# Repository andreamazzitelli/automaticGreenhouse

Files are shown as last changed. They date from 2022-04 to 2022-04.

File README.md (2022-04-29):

# automaticGreenhouse
This is the repository for the Internet of Thing 2021/2022 of the Master in Computer Science, La Sapienza Università di Roma

# General Description
The scope of the project is to create an automatic greenhouse that can act on the environment in which a plant is living to tailor the living space to the plant’s needs. By monitoring the environment, it’s possible to learn in real time the conditions in which the plant is living. In particular, the system measures those aspects that are fundamental to a plant, these being temperature, humidity and soil moisture. Knowing this information, the system can promptly act in several ways: opening or closing the water, turning on and off a heating lamp or by keeping the light always on. 

## Sensors
So to take the measurements needed by the system the following two sensors were selected:
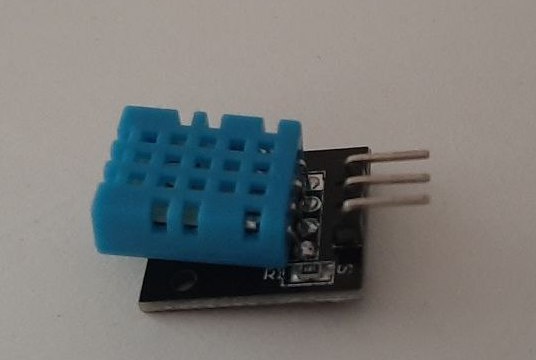
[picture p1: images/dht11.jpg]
dht11
- ***DHT11 Humidity and Temperature***: <br> this sensor collects information on the temperature and on the air’s humidity and gives them to the system using an analog output. In particular, for the temperature it has a range of 0-50°C with an accuracy of +/- 2°C with a precision of 8 bits; and for the humidity we have a range of 20-90% RH (RH stands for Relative Humidity) with an accuracy of +/- 5% RH with a resolution of 8 bits (the datasheet can be found here [DHT11 Datasheet](https://www.mouser.com/datasheet/2/758/DHT11-Technical-Data-Sheet-Translated-Version-1143054.pdf)).

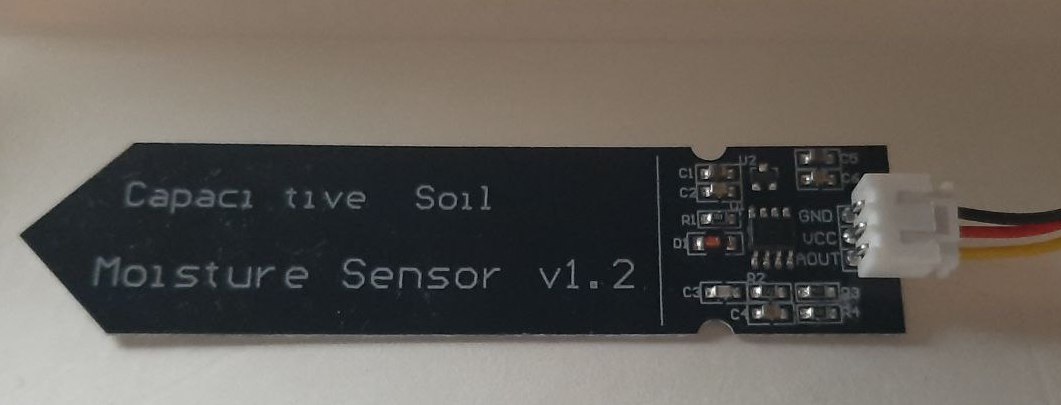
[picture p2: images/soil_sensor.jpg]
soil_sensot
- ***Soil Humidity Sensor***: <br> this sensor collects information on the soil moisture using capacitive sensing (i.e its capacitance changes depending on how much moisture is present in the soil), it gives its output to the system as analog input (the datasheet can found here [Soil Humidity Sensor Datasheet](https://cdn.shopify.com/s/files/1/1509/1638/files/Hygrometer_V1.2_Sensor_Modul_Datenblatt_AZ-Delivery_Vertriebs_GmbH.pdf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)).

The sensing done by the sensor is periodic because the system needs to continuously evaluate the environment in which the plant is living, indeed an event-driven one would not make sense taking into account the analogical nature of what the system measures (i.e temperature …). In particular the interval at which the sensors take their measurements is 15 seconds so that the system can always be updated without being overloaded with values.<br>
It is important that these sensors work independently even if the aspect they measure may depend on each other. For example air humidity may depend on the moisture in the soil but it also decreases with high temperature, for this reason the sensors must work in parallel to provide a correct and continuous evaluation of the environment. In the code this separation is achieved using threads.

## Actuators
To act on the environment the following two actuators were selected:
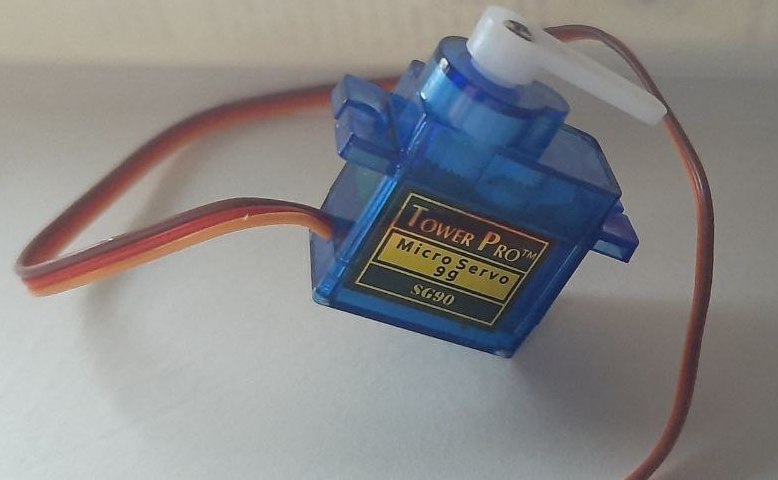
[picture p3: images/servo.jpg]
servo_motor
- ***Servo Motor SG90***: <br> the servo motor open and closes the water, for this reason it’s activation/deactivation depends on the values detected by the soil moisture sensor so to keep the humidity of the soil between 20% and 60% (that is the adequate percentage for most types of plants). More precisely the servo opens the water when the soil moisture gets lower than 20% and turn off the water when the moisture gets higher than 60%. (the datasheet can be found here [Servo Motor Datasheet](http://www.ee.ic.ac.uk/pcheung/teaching/DE1_EE/stores/sg90_datasheet.pdf))<br> To made use of a servo motor in this way I used the a 3D printed servo valve that can be found at this [LINK](https://www.thingiverse.com/thing:4876444),

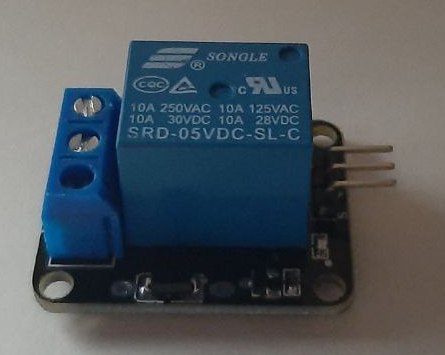
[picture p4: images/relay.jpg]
relay
- ***Relay Module 5V/250VAC***: <br>the relay instead can be used in several ways depending on what the user goal is, but in general is used to keep the temperature above a certain threshold by turning on and off a heating bulb. More precisely it is turned on if the temperature sensed by the dht11 sensor gets lower that (goal_temperature -10%) and is turned off if the value gets higher that (goal_temperature +10%). The +/- 10% are needed to avoid the relay to keep switching on and off due to very small changes in temperature (the datasheet can be found here: [Relay Datasheet](https://components101.com/switches/5v-single-channel-relay-module-pinout-features-applications-working-datasheet))

The activation or deactivation of these actuators can be done manually by the user, but by default is done in an automatic way. 

### Data Processed on the by the Board
In general the amount of the data received from the sensors depends on how well the threads that handle the measurement are synchronized. If they are perfectly in sync, then the system would receive a total of 24 bits (8 bits for temperature, 8 bits for relative humidity and 8 bits for soil moisture). <br><br>
This data is then formatted in a message that is then sent to the broker. In particular to reduce the number of bytes sent by the device in the network the message has a payload size of 9 bytes when sending data about temperature and humidity, and size of 5 bytes when sending data about soil moisture. Obviously in addition to the payload the message has a header but in this case is small thanks to the use of mqtt-sn protocol.

# System Architecture
In the following section the architecture of the whole system will be described starting from an overall view of the network components, then analyzing all the cloud aspects, and in conclusion there will be a brief description of how the sensors and actuators are connected to the board.
<br>
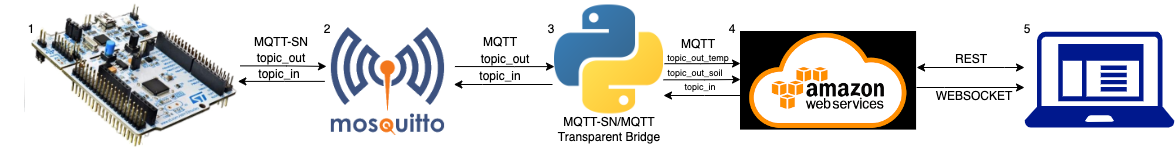
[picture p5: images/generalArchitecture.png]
generalArchitecture

<br>
The general architecture of the network can be described as a chain of blocks that exchange messages; this structure is shown in the image above. More in detail the block that compose the system are:
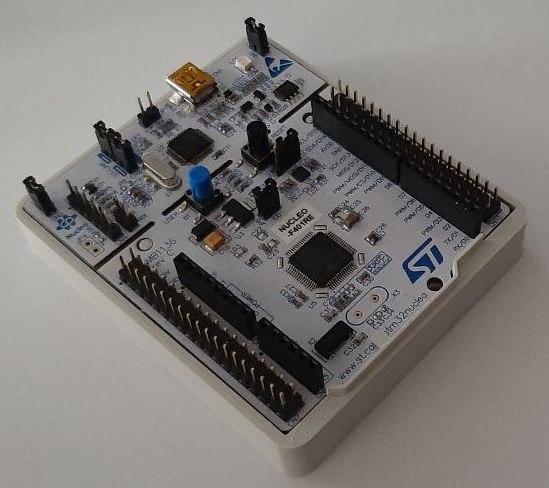
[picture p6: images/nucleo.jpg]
nucleo_board
1. ***Nucleo-f401re Board***: <br> it generates and sends data to the broker that is in the next block of the chain using mqtt-sn, it publishes the messages on the topic “topic_out”. Moreover it is subscribed to the topic “topic_in” of the broker in the next block where it reads the instructions that are sent by the user.

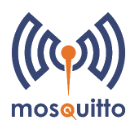
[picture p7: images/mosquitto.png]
mosquitto
2. ***MOSQUITTO***: <br> it is a MQTT-SN/MQTT message broker that is the closest block to the board. Indeed, it interacts directly with it. In particular it stores the messages coming from the board in the topic “topic_out” and those going to the board in the topic “topic_in”. In theory any mqtt-sn/mqtt broker can have this role.

3. ***MQTT-SN/MQTT TRANSPARENT BRIDGE***: python <br> it is a python script that works as a bridge exchanging messages using MQTT between the broker in the previous block and the broker on the cloud in the next block of the chain. <br><br> It is subscribed to both the topic “topic_in” of the cloud broker (in the next block) and to the topic “topic_out” of the previous block broker. Indeed when a message is published on the “topic_in” of the cloud broker the transparent bridge reads it and publishes it on the previous block’s broker. Something similar happens when a message is published on the “topic_out” of the previous block, the bridge reads this new publication and publishes it into the cloud broker. <br> <br>Regarding the publishing of messages in the adjacent blocks we have a peculiarity, this block performs some edge computation. Indeed it has the role of changing the format of the messages to make them more suitable for the blocks it is bridging. In particular it does the following: 
   - messages coming from the previous block and going to the next one, it expands them turning the small payload more suitable for a mqtt-sn communication into a proper json object so that the cloud functions can easily work with it.
   - messages coming from the next block and going to the previous one, it compresses the json object into a smaller message so to reduce the payload size so that it can consume less bandwidth and be easily handled by the previous block in the chain.<br><br>
Moreover we have another peculiarity in how the messages are published on the cloud mqtt broker indeed in this case the messages are published on two different topics of the cloud broker: “topic_out_temp” and “topic_out_soil” in this way is easier to separate and elaborate the messages coming from different sensors.

4. ***Amazon Web Services***: aws_logo<br> is the cloud part of the system. All the data received from the previous block on the topic “topic_out_temp” and “topic_out_soil” is processed, stored and then made available to the user using API REST. Moreover the user can send commands using API REST that publish the command on the topic “topic_in” of the cloud broker where it will be red by the previous block. (Obviously any cloud service provider correctly configured would work the same)

5. ***Web Application***: <br> last block of the chain. Allows the user to visualize the data collected by the system and interact with it. In particular using charts the user can see not only the measurements of the last hour but also see them almost in real time (we need to take into account the latency needed by the data to go from the board to the cloud services). Moreover some aggregated values are provided to the user like: the average, minimum and maximum values and the variation.

<div>
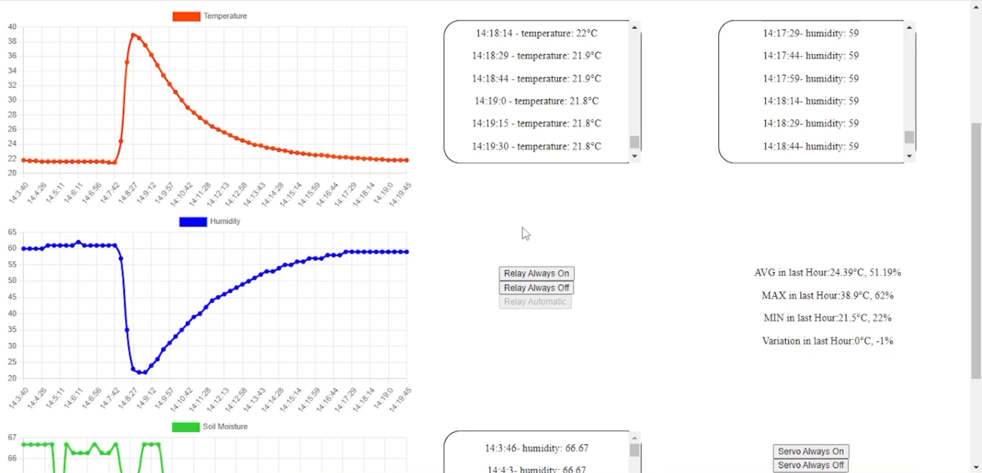
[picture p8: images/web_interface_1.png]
web1
   
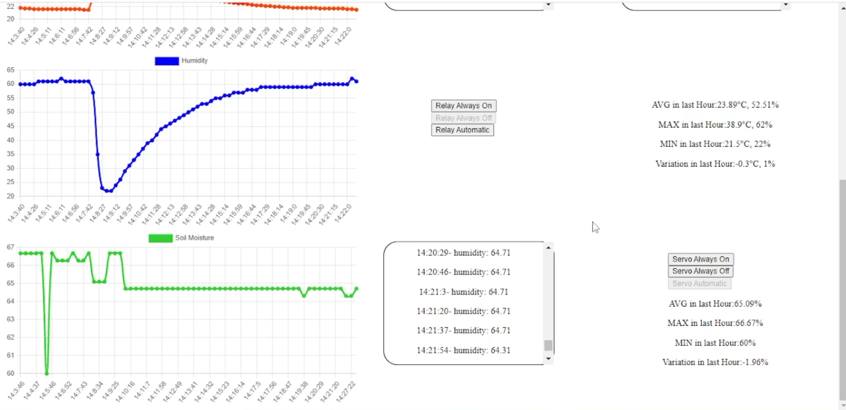
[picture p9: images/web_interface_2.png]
web2
   
</div>

### Cloud Services

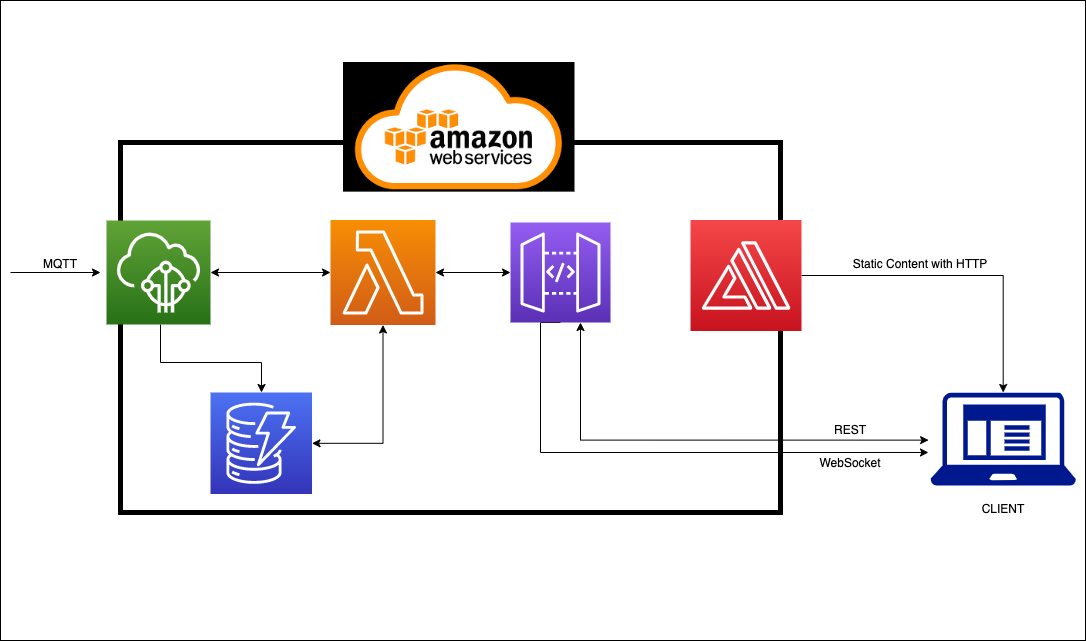
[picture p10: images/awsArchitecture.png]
awsArchitecture


As already mentioned the cloud service provider used is Amazon Web Services. In particular the services used are:
- ***Iot Core***: iot_core<br> whose main role is to work as a mqtt broker where messages are published. Moreover, the rule engine of the service allowed us to directly act on the incoming messages, saving them on the DB and invoking functions when a new message arrives.
- ***DynamoDB***: dynamoDB_logo<br> database where every data received from the board is stored. In particular it has 2 tables to store the information received and 1 used to keep track of the connections to the websocket service.
- ***Lambda***: lambda_logo<br> that allows us to write the functions for several purposes like: interact with the database, publish messages on a broker, handle the websocket (connection, disconnection and new information on the status). In particular it has 2 functions to read the data of the sensors (one per table), 1 function to publish messages on a broker, 3 functions to handle the websocket.
- ***API Gateway***: api_gateway<br> to create and publish both the REST API and the WebSocket API
- ***AWS Amplify***: amplify<br> to provide the web application’s static content to the user 

<br><br>
***NOTE: on april 2022 AWS introduced the Lambda Function URLs that makes the use of API Gateway not strictly needed. Indeed is possible to use this new functionality to obtain an endpoint for a Lambda function and directly call the function skipping the creation of a new API, at least for the REST ones. In theory is easy to introduce Lambda URLs in this project simply by subbstituting the call to the Gateways' APIs with a call the the Lambda URL but futher testing would be required*** <br><br>

Now is possible to analyze the interaction with AWS from the point of view of the IoT Core broker receiving a message and from the one of a user accessing the web interface. <br>In the former we have that once the broker receives a message, it is received either on the “topic_out_temp” or on the “topic_out_soil” topic, in both cases two things happens: the information is stored in the corresponding table and the lambda function sends a messages with the data to all active connections on the websocket.<br><br> In the latter we have that the user asks to AWS Amplify using https for the static components of the web application, as soon as these are loaded the javascript in the web page does two things: invokes the REST API to obtain the data stored in the DynamoDB tables and connects to the websocket provided by an API of the API Gateway. <br>In this way the client has the data from the last hour and is kept updated thanks to the websocket. <br>Moreover from the web application the user has the ability by pressing some buttons to invoke an API that invokes a lambda function that publishes a message with a command to the board on the cloud broker.

### Connections to the Board
[Here](https://github.com/andreamazzitelli/automaticGreenhouse/raw/main/images/automaticGreenhouseCircuit.fzz) the link to fritzing circuit 
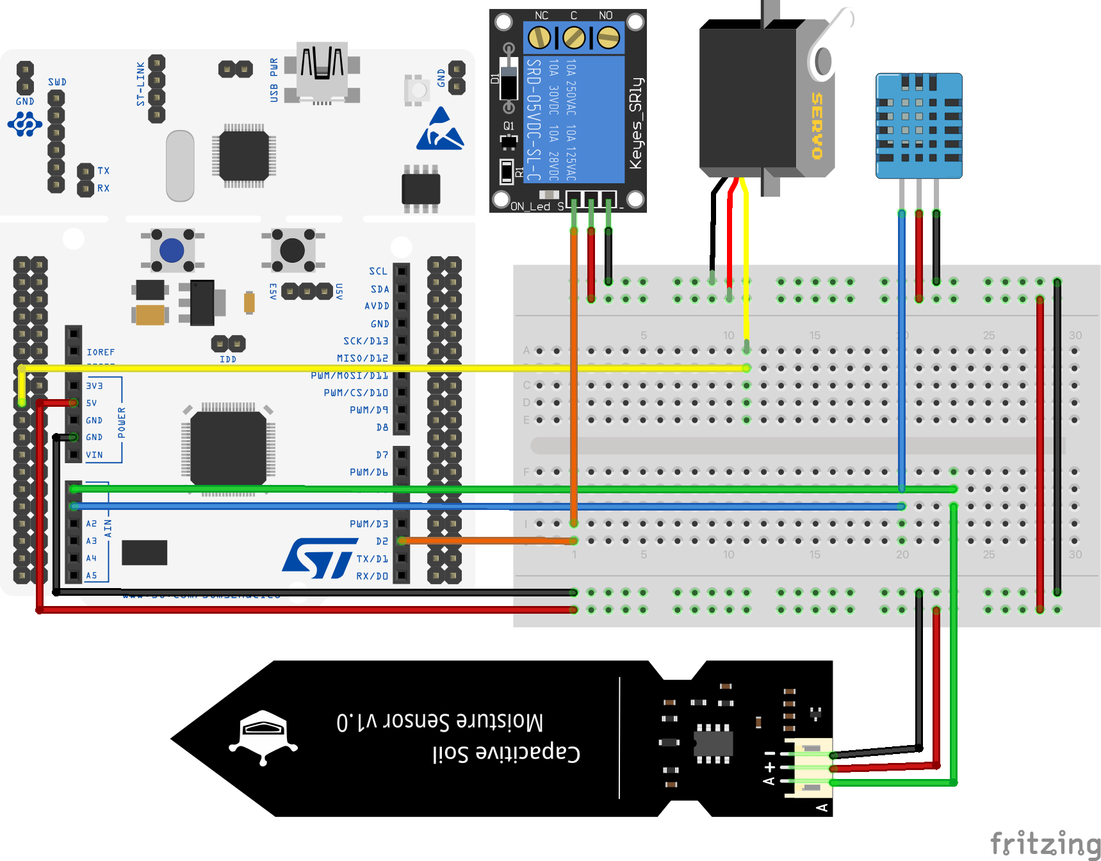
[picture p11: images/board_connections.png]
board connections

So to conclude this section a brief description on how the board, sensors and actuator are connected. The connections are rather simple as is possible to see from the above image:

pin board<br>

- All the sensors and actuators are connected to Ground and 5V
- the relay module is connected to the digital pin Arduino pin D2(PA10 on the board)
- the servo motor is connected to the pin PA15 a PWM pin
- the dht11 sensor is connected to analog pin A1
- the capacitive soil moisture sensor is connected to analog pin A0 

(the position of the pins on the board can be see on the pinout image on the left)<br>
Obviously the board is connected to a laptop so that it can get power and use the ethos (ethernet-over-serial)  mechanism.

### Network Performances
Using a tool to analyze packets in the network (like wireshark) is possible to see how the network is affected by the message exchanged by the several components. Indeed the most problematic part of the connection is the link between the board and the mosquitto broker. In particular we have that the network traffic happening using UDP between these two components is:
- 33 bytes for sending data from the soil moisture sensor 
- 37 bytes for sending the data from the dht11 sensor. 

Assuming that the threads handling these measurements are synchronized we can say that a total of circa 16,8 kb per hour are generated and the needed bandwidth to run the system is of at least 4,7 bytes per second. <br><br>
Even if the bandwidth required to run the system is low for today's standards in some situations it may be needed to reduce even more the data transmitted. This is achievable if the transmission interval is increased, but in this the data collected on the cloud is less representative of the real state of the environment. To avoid this loss in accuracy the system could aggregate data on the node, for example at every timeout it does not send the last value sensed by the sensor but the average of the previous interval. So there is a clear tradeoff between the amount of data transmitted on the network and the system’s accuracy.<br><br>
The other link of interest is the one between the mosquitto broker and the cloud service provider. The main aspect here is that in the middle there is the transparent bridge that acts on the messages. However even if the message size increases and the protocol used to exchange messages is TCP (that uses in general more messages than UDP), the operation done by the transparent bridge are done on the edge. For this reason, the presence of a more reliable bandwidth is almost guaranteed.<br><br>
***Latency***: instead regarding the latency of the system we have that usually is under 2s from when the sensor register a new value and to when this new value appears on the web application, the same is true for the other direction: there is a latency under 2s from when a button is clicked on the web app to when the system acts accordingly. <br>This latency in a case like this is not a problem at all, indeed the system does not have strict requirements neither on how fast to act when a command is sent by the user nor on how fast the data must be shown to the user. Mainly this is due to what the system is though for, indeed under normal circumstances is rare for values like temperature and humidity to drastically change and even if we are in those rare circumstances, excluding the user response time, 4s is small enough to prevent "damages".

# WALKTHROUGH
The first steps to do are:
- download and setup RIOT OS as described in the official documentation ([RIOT OFFICIAL DOCUMENTATION](https://doc.riot-os.org/getting-started.html))
- download and setup the mosquitto broker as described in the official documentation ([DOCUMENTATION](https://github.com/eclipse/mosquitto.rsmb))
- download this repository

### Cluod Setup
- ***DynamoDB***: create 3 tables: 
   1. connection_table with Partition Key a string called“connection_id”
   2. soil_humidity_table with Partition Key a number called “id”
   3. temperature_table with Partition Key a number called “id”
- ***Lambda***: create 6 lambda functions choosing as language Node.js 14.x where to paste the code provided in this repository under the aws directory (see later for a brief description on how to add permission to a lambda function):
   1. connect: where to paste the code found in aws/connect.js and needs to have permission to access to DynamoDB
   2. disconnect: where to paste the code found in aws/disconnect.js and needs to have permission to access to DynamoDB
   3. publish2Broker where to paste the code found in aws/publish2Broker.js and and needs to have permission to access to IoT
   4. readTemeperature: where to paste the code found in aws/readTemperature.js and needs to have permission to access to DynamoDB
   5. readSoilHumidity: where to paste the code found in aws/readSoilHumidity.js and needs to have permission to access to DynamoDB
   6. readTemp4WebSocket: where to paste the code found in aws/readTemp4WebSocket.js and needs to have permission to access to DynamoDB, API Gateway and Execute API<br>
***NOTE: is fundamental to properly set up the permissions given to each function***

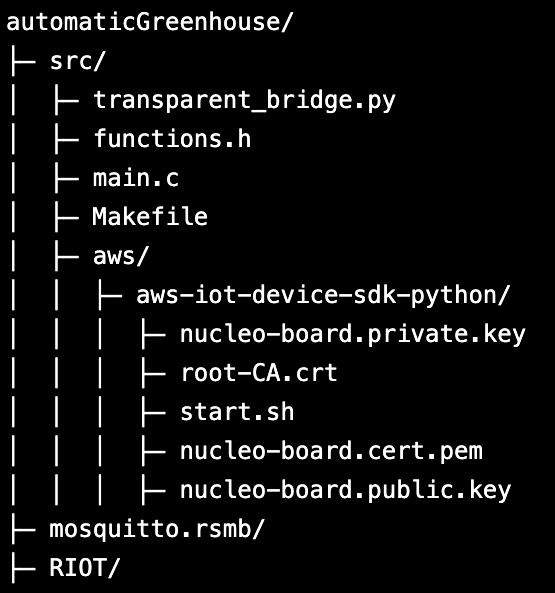
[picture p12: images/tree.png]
pin board
- ***IotCore***: click on “Connect a device” and follow the steps using as name of the thing "nucleo-board", at the end of the guided procedure it should have downloaded the following files: root-CA.crt, nucleo-board.cert.pem, nucleo-board.private.key. 
Now for the system to work build a directory like the one in the image on the right (all the file in the aws directory were downloaded after this first step of the IoTCore)
<br>
Now always from the IoT Core you need to go on Secure->Policies->nucleo-board-Policy then click on “Edit Active Policy” and append in the policy resource text area:
- in the first one: resource_arn:topic/topic_out_soil,resource_arn:topic/topic_out_temp,resource_arn:topic/topic_in (elements MUST be separate with a comma WITHOUT spaces in between),
- in the second one: resource_arn:topicfilter/topic_in,
- in the third one: resource_arn:client/nucleo,
Once this is done click on “Save as new version” and set it as active one. <br>

The next step is to configure the rules of the rule engine so go on Act->Rules, here you need to create two rules:
   - in the first one set the “Rule query statement” as “SELECT temperature, humidity FROM 'topic_out_temp' “ and add the action to “insert a message into DynamoDB” giving as table name “temperature_table”, Partition key “id” and as Partition Key Value “$(timestamp())” (this will create a new element in the table with id the epoch time). Once this action has been added click again “Add Action” and select “Send message to Lambda Function” selecting as lambda function readTemp4WebSocket
   - in the second one set the “Rule query statement” as “SELECT soil_humidity FROM 'topic_out_soil'”, also here add the same action as the other rule changing only the table name in “soil_humidity_table”

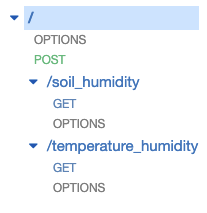
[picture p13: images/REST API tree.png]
rest api tree
- ***API Gateway***: there are 2 APIs needed:<br>
   - a WebSocket API called “sensors” with 4 routes each calling a lambda function: $connect that calls “connect”, $disconnect that calls “disconnect”, readTemp that calls “readTemp4WebSocket” and readSoil that also calls “readTEmp4WebSocket”.
   - a REST API also called sensors that has the structure in the image. In particular the POST on / should call the "publish2Broker" function, the GET on /soil_humidity should call "readSoilHumidity", the GET on /temperature_humidity should call "readTemperature". (take note of which are the endpoints of these resources because, because there will be needed on a later step)

- ***AWS Amplify***: first you need to edit the file index.html changing adding the link to your API in the following lines:
   - 372, inside the fetch add as a string the URL to the API that returns the values obtained from the dht11 sensor,
   - 382, inside the fetch add as a string the URL to the API that returns the values obtained from the soil moisture sensor,
   - 451 as first parameter inside the fetch add as a string the URL to the API that allows us to send commands to the board.
   
   Once this is done create a new project and load the index.html, index.js and style.css files that you find inside the directory web app of this repository

With this the AWS setup is done.

### Board Setup
The next steps are:
- connect the sensors to the board like shown in the previous image.
- connect the board to you machine
<br>
Now go to the mosquitto.rsmb/rsmb/src folder and execute the following command:

```
./broker_mqtt config.conf
```

and leave the broker running. <br>
Open a new terminal on MAIN/automaticGreenhouse and open the transparent_bridge.py and set the lines 8-11 to the requested value, save and close. Then execute:

```
python3 transparent_bridge.py
```

as before leave the bridge running and open a new terminal in the same  folder and execute 

```
make flash term
```

once the command is done i.e the serial monitor is shown, open a new terminal and execute the following command 

```
sudo ip a a 2000:2::1 dev tap0
```

then press the reset button on the board and after a few seconds if everything has been set up correctly the board should start to operate and on the 
application the measurement should be showing.

# BLOG POST: 
I decided to focus a specific aspect of the project: how to connect the nucleo-f401re to the cloud. <a href="https://www.hackster.io/mazzitelli1835022/connect-riot-os-with-the-cloud-4bf88a">Here's the link to the blogpost</a>
# Linkedin:
Here is my <a href="https://www.linkedin.com/in/andrea-mazzitelli/">Linkedin Account</a>
# YouTube Video:
To provide a better overview of the system and it's functionalities. The demo is not done in a real environment (i.e with sensors/actuators put inside a real greenhouse) becuase the phenomenon that the system sense usually does not drastically change in a brief period of time (both temperature and soil moisture need sometimes to increase or decrease). So for sake semplicity in showing the result, in the demo I manully alter the values sensed by either using an hairdryer on the temperature sensor or by forcing the soil moisture sensor to sense lower level of moisture.
Here is the link to the demo: <a href="https://youtu.be/zmuy0vqKZXE">YouTube Video</a>

# Photos
<div>
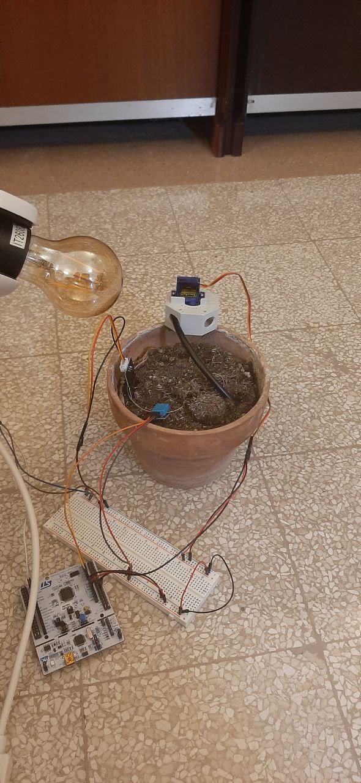
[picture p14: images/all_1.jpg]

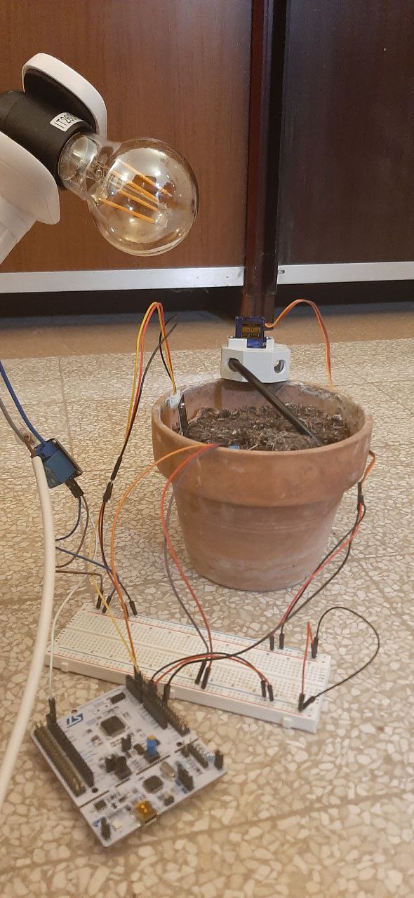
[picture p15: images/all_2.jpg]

</div><br>
<div>
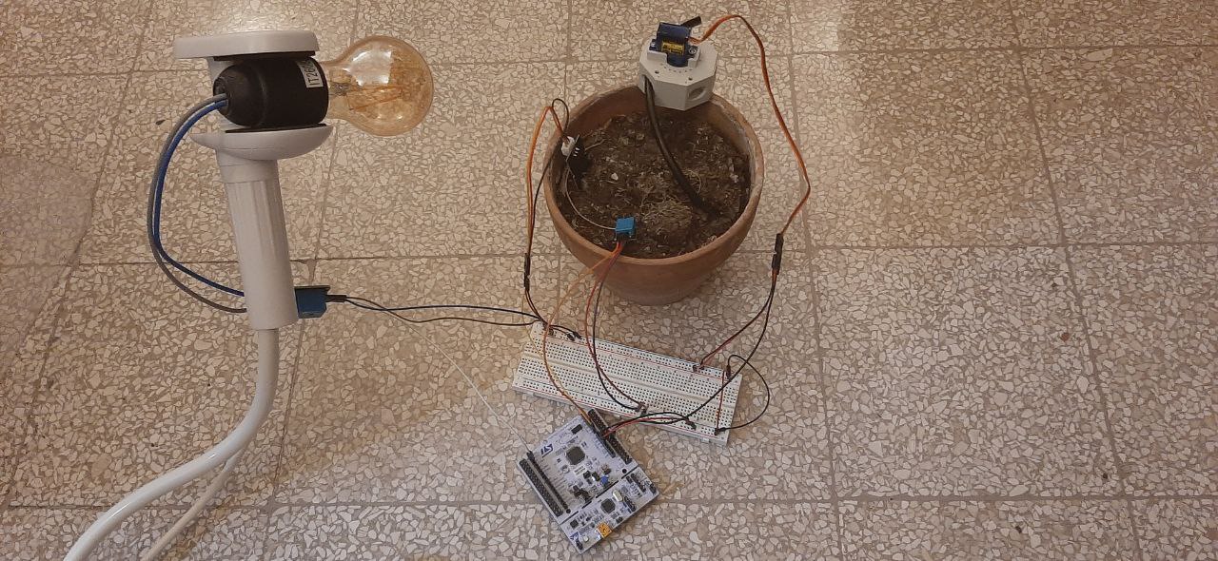
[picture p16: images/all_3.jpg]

</div><br>
<div>
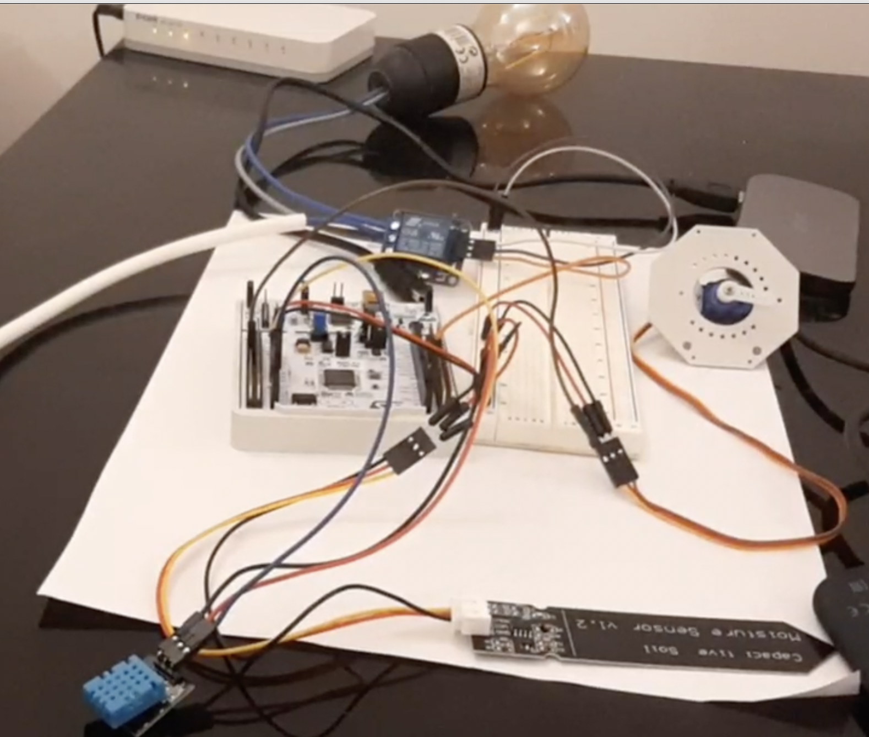
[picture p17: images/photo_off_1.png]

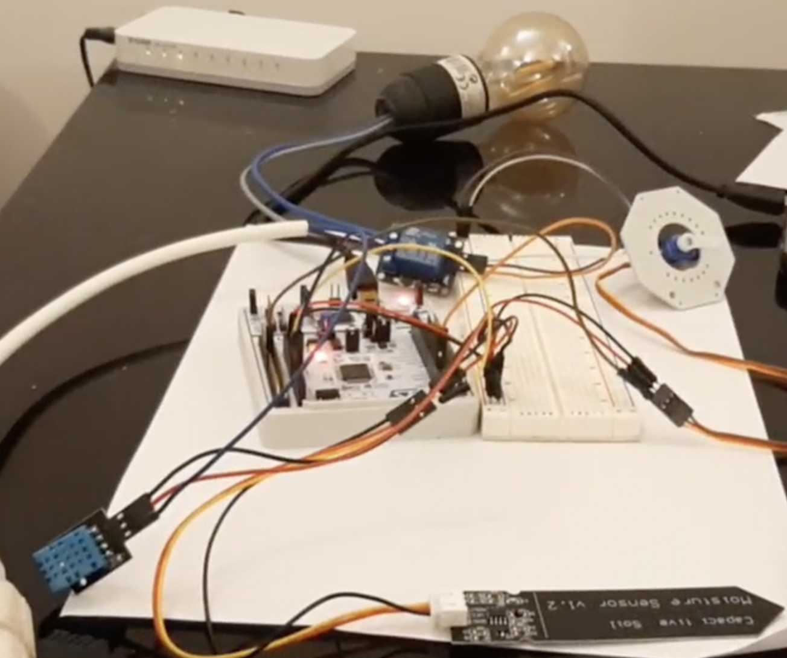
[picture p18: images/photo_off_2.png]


</div><br>
<div>
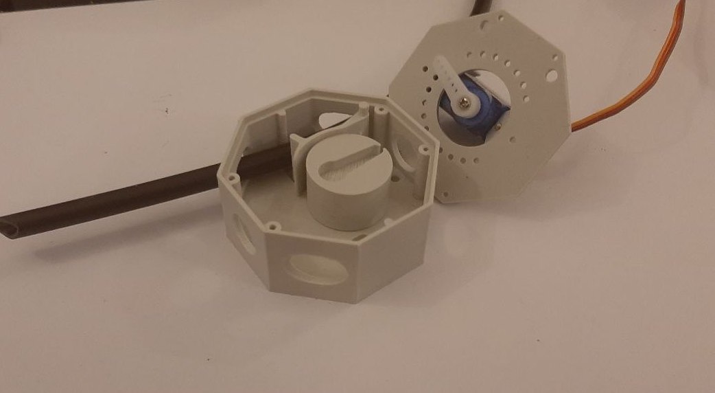
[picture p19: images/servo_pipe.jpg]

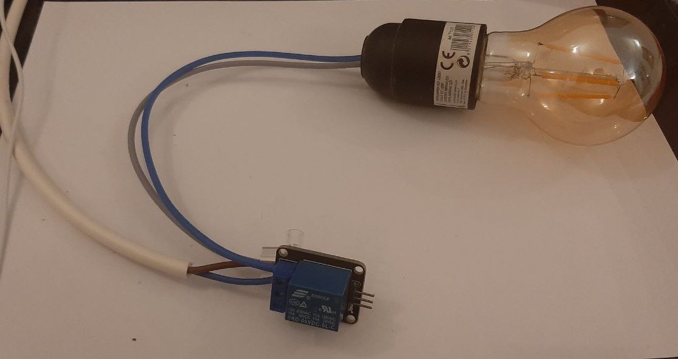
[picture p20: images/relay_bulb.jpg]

</div><br>

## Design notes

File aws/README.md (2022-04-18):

# AWS
in this directory you can find all the code for the lambda function. In some of them must be added some information relative the the aws account (i.e region of the resource).

Moreover make sure to grant the following permissions (to easy the process simply grant the function all the permissions to the service):
- connect: write on table connection_table of DynamoDB
- disconnet: write on table connection_table of DynamoDB
- publish2Broker: publish messages on IoT Core
- readSoilHumidity: read table soil_humidity_table of DynamoDB
- readTemp4WebSocket: read table connection_table of DynamoDB, access to API Gateway and Execute API (NOTE: even if the name of this function suggests that is only for the temperature and humidity messages, indeed is also for soil_humidity ones)
- readTemperature: read table temperature_table of DynamoDB

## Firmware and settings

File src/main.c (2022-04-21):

//Importing Standard C Libraries
#include <stdio.h>
#include <string.h>
#include <stdlib.h>

//Importing my functions
#include "functions.h"

//Importing General Purpose Libraries
#include "xtimer.h"
#include "thread.h"

//Importing Libraries for Emcute and Networking
#include "msg.h" //mi sa che non serve
#include "net/emcute.h"
#include "net/ipv6/addr.h"

//Importing Libraries for Servo Motor
#include "periph/pwm.h"
#include "servo.h"

//Importing Libraries for DHT11 Sensor
#include "fmt.h"
#include "dht.h"
#include "dht_params.h"

//Importing Libraries for Relay
#include "periph/gpio.h"

//Importing Libraries for Soil Moisture Sensot
#include "periph/adc.h"


//Definitions for Servo
#define DEV         PWM_DEV(0)
#define CHANNEL     0
#define SERVO_MIN        (900U)
#define SERVO_MAX        (2500U)

//Definitions for Relay
#define RELAY_ON ("ON")
#define RELAY_OFF ("OFF")

#ifndef GOAL_TEMP
#define GOAL_TEMP 200
#endif

//Definitions for Soil Moisture Sensor
#ifndef ANALOG_LINE
#define ANALOG_LINE (ADC_LINE(0))
#endif
#define RES ADC_RES_8BIT //analog read resolution
#define MAX_HUMIDITY (255)

//Definition for Emcute and MQTT Broker
#ifndef EMCUTE_ID
#define EMCUTE_ID           ("nucleo-board")
#endif
#define EMCUTE_PRIO         (THREAD_PRIORITY_MAIN - 1)

#define NUMOFSUBS           (16U)
#define TOPIC_MAXLEN        (64U)

#define SERVER_ADDR ("2000:2::1")
#define SERVER_PORT 1885
#define IPV6_PREFIX_LEN (64U)

#define DEFAULT_INTERFACE ("4")
#define DEVICE_IP_ADDR ("2000:2::2")

#define MQTT_TOPIC_OUT "topic_out"
#define MQTT_TOPIC_IN "topic_in"
#define MQTT_QoS (EMCUTE_QOS_0)

//Definition of Array used as Stack by threads
static char stack[THREAD_STACKSIZE_DEFAULT];
static char temperature_stack[THREAD_STACKSIZE_DEFAULT];
static char soil_stack[THREAD_STACKSIZE_DEFAULT];

//Definition of Emcute Data Structure
static emcute_sub_t subscriptions[NUMOFSUBS];

//Definitions of Servo Motor Data Structure and needed variables
static servo_t servo;
static bool servo_open = false;
static int humidity_upper_bound = (int)(MAX_HUMIDITY*0.2);
static int humidity_lower_bound = (int)(MAX_HUMIDITY*0.6);
static bool servo_always_on = false;
static bool servo_always_off = false; 

//Definitons the Pins for Relay and Soil Moisture Sensor
static gpio_t pin_out = GPIO_PIN(0, 10);
static adc_t pin_in = ANALOG_LINE;

//Definitions of DHT11 Data Structure and needed variables
static dht_t dev;
static int16_t goal_temp = GOAL_TEMP
static bool relay_state = false;
static bool relay_always_on = false;
static bool relay_always_off = false;

//Function called when a message is published on the topic the board is subscribed
static void on_pub(const emcute_topic_t *topic, void *data, size_t len){
    (void)topic;
    (void)len;
    char *in = (char *)data;

    //printf("Received:%s\n", in);
    //printf("### got publication for topic '%s' [%i] ###\n",
    //       topic->name, (int)topic->id);

    if(*in == 'g'){ 
        goal_temp = (int16_t)atoi((in+1));
        printf("%d\n", goal_temp);
    }
    else if(*in == 's'){
       if(*(in+1) == '1'){ //request to keep the servo always open
           servo_always_on = true;
           servo_always_off = false;
           //printf("%d,%d\n", servo_always_on, servo_always_off);
       }
       else if(*(in+1) == '0'){ //request to keep the servo always close
           servo_always_on = false;
           servo_always_off = true;
           //printf("%d,%d\n", servo_always_on, servo_always_off);
       }
       else{ //request to keep the servo always automatic
           servo_always_on = false;
           servo_always_off = false;
           //printf("%d,%d\n", servo_always_on, servo_always_off);
       }
       servo_change_pos();
   }
   else if(*in == 'r'){
       if (*(in+1) == '1'){ //request to keep the relay always open
           relay_always_on = true;
           relay_always_off = false;
       }
       else if(*(in+1) == '0'){ //request to keep the relay always close
           relay_always_on = false;
           relay_always_off = true;

       }
       else{ //request to keep the relay always automatic
           relay_always_on = false;
           relay_always_off = false;
       }
       change_relay_state("");
   }
   return;
}

//Function for the emcute thread
static void *emcute_thread(void *arg)
{
    (void)arg;
    emcute_run(CONFIG_EMCUTE_DEFAULT_PORT, EMCUTE_ID);
    return NULL;    /* should never be reached */
}

//Function that setup the address on the board
static int address_setup(char *name, char *ip_address){

    netif_t *iface = netif_get_by_name(name); //getting the interface where to add the address
    if(iface == NULL){
        puts("No such Interface");
        return 1;
    }

    ipv6_addr_t ip_addr;
    uint16_t flag = GNRC_NETIF_IPV6_ADDRS_FLAGS_STATE_VALID | (IPV6_PREFIX_LEN << 8U); //setting the flag for the set function
    
    //Parsing IPv6 Address from String 
    if(ipv6_addr_from_str(&ip_addr, ip_address) == NULL){
        puts("Error in parsing ipv6 address");
        return 1;
    }

    //Set Interface Options 
    if(netif_set_opt(iface, NETOPT_IPV6_ADDR, flag, &ip_addr, sizeof(ip_addr)) < 0){
            puts("Error in Adding ipv6 address");
            return 1;
        }
    printf("Added %s with prefix %d to interface %s\n", ip_address, IPV6_PREFIX_LEN, name);
    return 0;
}

//Function to connect to the Broker
static int connect_broker(void){
    sock_udp_ep_t gw = { .family = AF_INET6, .port = SERVER_PORT }; //creating the socket
    char *topic = NULL;
    char *message = NULL;
    size_t len = 0;
    
    //Parsing IPv6 Address from String
    if (ipv6_addr_from_str((ipv6_addr_t *)&gw.addr.ipv6, SERVER_ADDR) == NULL) {
        printf("error parsing IPv6 address\n");
        return 1;
    }

    //Connecting to brokee
    if (emcute_con(&gw, true, topic, message, len, 0) != EMCUTE_OK) {
        printf("error: unable to connect to [%s]:%i\n", SERVER_ADDR, (int)gw.port);
        return 1;
    }

    printf("Successfully connected to gateway at [%s]:%i\n",
           SERVER_ADDR, (int)gw.port);

    //Setting Up the subscription
    subscriptions[0].cb = on_pub;
    subscriptions[0].topic.name = MQTT_TOPIC_IN;

    //Subscribing to topic
    if (emcute_sub(&subscriptions[0], MQTT_QoS) != EMCUTE_OK) {
        printf("error: unable to subscribe to %s\n", subscriptions[0].topic.name);
        return 1;
    }

    printf("Now subscribed to %s\n", subscriptions[0].topic.name);

    return 0;
}

//Function to publish on the broker
static int publish(char *t, char *message){
    emcute_topic_t topic;
    topic.name = t;
    //printf("%s lunghezza %d\n", message, strlen(message));
    if(emcute_reg(&topic) != EMCUTE_OK){ //getting ID from the topic
        printf("cannot find topic:%s", topic.name);
        return 1;
    }

    if(emcute_pub(&topic, message, strlen(message), MQTT_QoS) != EMCUTE_OK){ //publishing on the broker
        printf("cannot publish data\n");
        return 1;
    }
    //printf("published message: %s (%i) on topic %s (id:%i)",
    //    message, (int)strlen(message), topic.name, topic.id);
    return 0;

}

//Function to change the servo's positions
static void servo_change_pos(void){
    //printf("In change servo %d, %d\n", servo_always_on, servo_always_off);
    if(servo_always_on){
        if(servo_open)return;
        else{
            servo_set(&servo, 2*SERVO_MIN);
            servo_open = true;
            return;
        }
    }
    else if(servo_always_off){
        if(!servo_open)return;
        else{
            servo_set(&servo, 0);
            servo_open = false;
            return;
        }
    }
    if(servo_open){
        servo_set(&servo, 0);
        servo_open = false;
        return;
    }
    else{
        servo_set(&servo, 2*SERVO_MIN);
        servo_open = true;
        return;
    }

}

//Function that Initialize all Sensors and Actuators
static int sensor_init(void){

    if(servo_init(&servo, DEV, CHANNEL, SERVO_MIN, SERVO_MAX)){
        printf("Failed to Init Servo");
        return 1;
    }
    servo_set(&servo, 0); //resetting servo position at startup
    puts("Servo Initialized");

    if(dht_init(&dev, &dht_params[0])){
        printf("Failed Init DHT");
        return 1;
    }
    puts("DHT11 Initialized");

    if (gpio_init(pin_out, GPIO_OUT)) {
        puts("Failed to Init Relay's Pin");
    }
    puts("Relay's Pin Initialized");
    
    if(adc_init(pin_in)){
        puts("Failed to Init Analog Line");
    }
    puts("Analog Line Init");

    return 0;
}

//Function to change the relay status
static void change_relay_state(char *status){
    if(relay_always_on){
        if(relay_state)return;
        else{
            gpio_set(pin_out);
            relay_state = true;
            return;
        }
    }
    else if(relay_always_off){
        if(!relay_state)return;
        else{
            gpio_clear(pin_out);
            relay_state = false;
            return;
        }
    }

    if(relay_state && strcmp(status, RELAY_OFF)==0){
        //puts("relay off");
        gpio_clear(pin_out);
        relay_state = false;
        return;
    }
    else if(!relay_state && strcmp(status, RELAY_ON)==0){
        //puts("relay on");
        gpio_set(pin_out);
        relay_state = true;
        return;
    }


}

//Function executed on the thread that handles the measurement of temperature and humidity
void *temp_relay_logic(void *arg){

    (void)arg;
    while(1){
        int16_t temp, hum;
        dht_read(&dev, &temp, &hum); //reading values from sensor
        //printf("DHT values - temp: %d.%d°C - relative humidity: %d.%d%%\n",temp, temp%10, hum/10, hum%10);
        if(temp > goal_temp*1.1)change_relay_state(RELAY_OFF);
        else if(temp <= goal_temp*0.9)change_relay_state(RELAY_ON);

        //setting up message to send
        char message[9];    
        sprintf(message,"t%dh%d", temp, hum);
        publish(MQTT_TOPIC_OUT, message); //publishing message on broker

        xtimer_sleep(15); //sleeping

    }
    return NULL;
}

//Function executed on the thread that handles the measurement of soil moisture
void *soil_water_logic(void *arg){
    (void)arg;
    int soil_hum;
    
    while (1)
    {
        soil_hum = adc_sample(pin_in, RES); //reading values from sensor

        if(soil_hum < 0)printf("Error in Sampling");
        else if(soil_hum > humidity_upper_bound && servo_open){
            servo_change_pos();
        }
        else if(soil_hum < humidity_lower_bound && !servo_open){
            servo_change_pos();
        }

        //setting up message to send
        char message[5];
        sprintf(message, "s%d", soil_hum);

        publish(MQTT_TOPIC_OUT, message); //publish message on broker

        xtimer_sleep(15); //sleeping time
    }
    return NULL;    
}

//Main
int main(void){

    puts("Starting Up\n");

    //Setting memory for the subscription list
    memset(subscriptions, 0, (NUMOFSUBS * sizeof(emcute_sub_t)));

    //Starting Emcute Thread
    thread_create(stack, sizeof(stack), EMCUTE_PRIO, 0,
                  emcute_thread, NULL, "emcute");
    printf("Emcute Thread Started\n");
    
    // Adding GUA to the interface 
    if(address_setup(DEFAULT_INTERFACE, DEVICE_IP_ADDR)){
        printf("Impossible to set up the interface\n");
        return 1;
    }
    
    //Connecting to broker and subscribing to topics*/
    if(connect_broker()){
        printf("Impossible to Connect Correctly with the Broker\n");
        return 1;
    }

    //Initializing Sensors
    if(sensor_init()){
        printf("Failed to Initialize Sensors\n");
        return 1;
    }
    
    //Starting Thread that handles temperature and humidity measurement
    thread_create(temperature_stack, 
                sizeof(temperature_stack),
                THREAD_PRIORITY_MAIN - 1, 0,
                temp_relay_logic, NULL, "temp_relay_logic");
    puts("Temperature Thread Started");

    //Starting Thread that handles soil moisture measurement
    thread_create(soil_stack,
                sizeof(soil_stack),
                THREAD_PRIORITY_MAIN -1, 0,
                soil_water_logic, NULL, "soil_water_logic");
    puts("Soil Thread Started");

    /*Never to be reached*/
    return 0;
}

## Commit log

2022-04-13 add servo motor image
2022-04-13 add relay image
2022-04-13 add board connections image
2022-04-26 fritzing diagram
    [automaticGreenhouseCircuit.fzz]
